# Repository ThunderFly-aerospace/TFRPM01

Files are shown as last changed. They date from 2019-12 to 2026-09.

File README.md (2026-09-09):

<a href="https://certification.oshwa.org/cz000009.html" title="Open Source Hardware Association Certificate">Open Source Hardware Association Certificate</a>

# TFRPM01 - RPM Measuring UAV Avionics Device

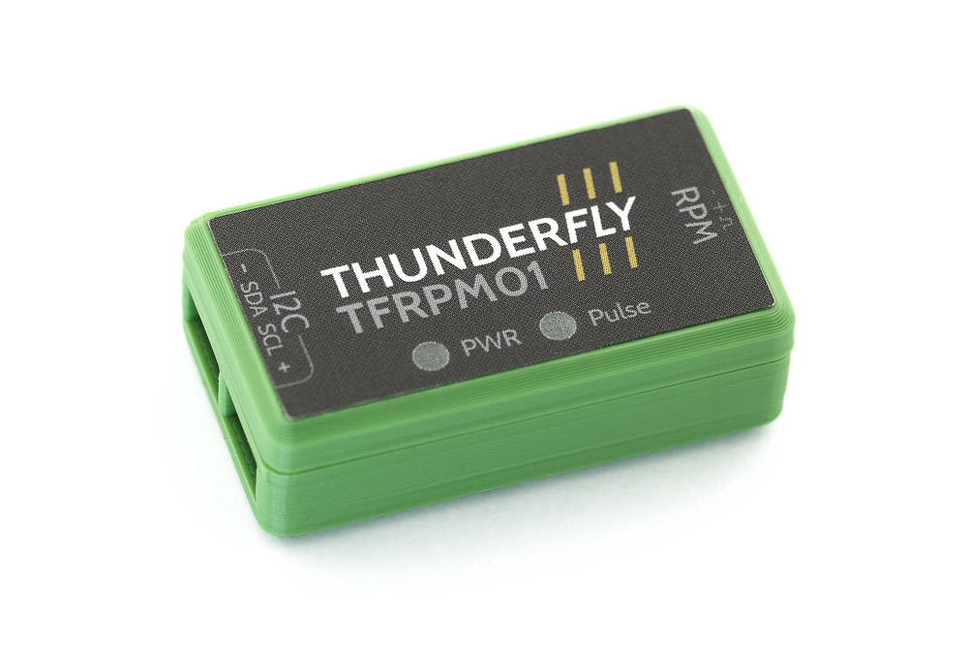
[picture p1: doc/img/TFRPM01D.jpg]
Top view on I2C RPM sensor


## Overview
The TFRPM is designed to measure revolutions per minute (RPM) in UAVs. It connects directly to Pixhawk controllers like CUAV V5+ or Holybro Pixhawk 6X via a [standard I²C connector](https://github.com/pixhawk/Pixhawk-Standards/blob/master/DS-009%20Pixhawk%20Connector%20Standard.pdf) and has the driver in PX4 firmware.

## Specifications

### Features
- **Schmitt Trigger Input**: To shape non-uniform signals from RPM sensing elements.
- **Self-Counting and Memory**: Offloads the flight controller's MCU.
- **LED Indicator**: Optionally visible in daylight for input status.
- **Protection**: Short-circuit protection on the probe connector.
- **I²C Connectors**: Pass-through connectors for daisy-chaining sensors.
- **Design**: Robust and repairable.

### Technical Parameters
- **Pulse Frequency Range**: 0 - 20 kHz.
- **I2C Connector**: 2x 4-pin JST-GH.
- **RPM Connector**: 3-pin 2.54mm pitch header.
- **I2C Address**: 0x50 default, alterable to 0x51.
- **Operating Temperature**: −20°C to +40°C.
- **Input Voltage**: +3.6V to +5.4V.
- **Mass**: 12g (4g PCB + 8g case).
- **Dimensions**: Case - 23.5x42x12.5mm, PCB - 37.5x19mm.
- **Weather Resistance**: IP40.

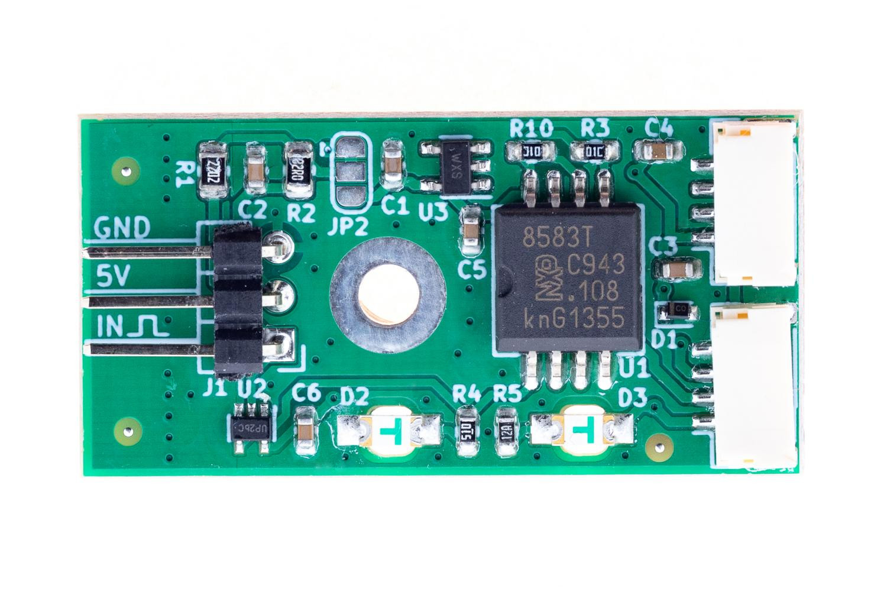
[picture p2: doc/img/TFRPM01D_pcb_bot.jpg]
Bottom view on I2C RPM sensor




### Where to Get It?
TFRPM can be bought directly from ThunderFly via [email contact](https://www.thunderfly.cz/contact-us.html). The email can also be used if there are specific requirements for custom modifications or if the product will be inquired in significant quantities. TFRPM is also available for online purchase through the [Tindie store](https://www.tindie.com/products/thunderfly/tfrpm01-drone-rpm-tachometer-sensor/).

### Connection to Pixhawk Autopilot
Follows the [Pixhawk connector standard](https://github.com/pixhawk/Pixhawk-Standards/blob/master/DS-009%20Pixhawk%20Connector%20Standard.pdf) with specific color coding.

### I²C Address Configuration
The default address is 0x50, changeable to 0x51.

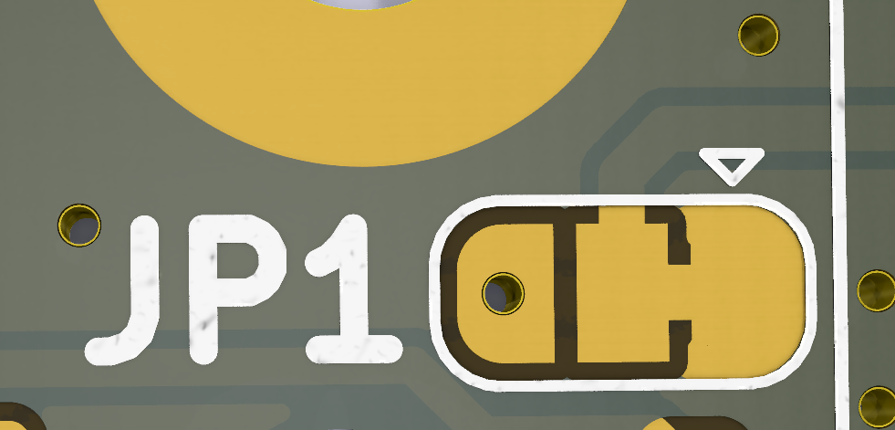
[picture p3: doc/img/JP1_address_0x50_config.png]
The default 0x50 address setup


### Mounting Options
The device can be mounted with or without a provided 3D-printed case.

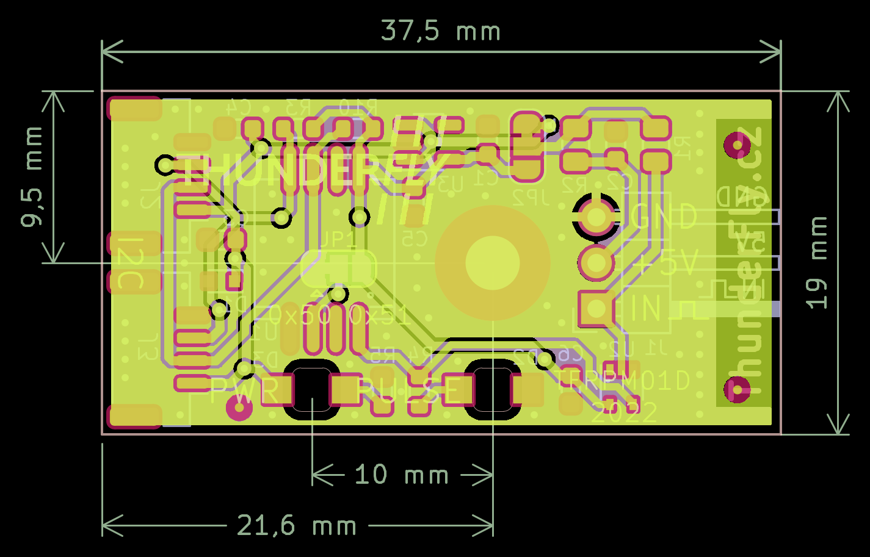
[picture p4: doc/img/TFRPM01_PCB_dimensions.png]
TFRPM01 PCB dimensions


### Sensor Probe Selection

Compatible with multiple probe types, including Hall effect and optical probes. See the [TFPROBE01](https://github.com/ThunderFly-aerospace/TFPROBE01) and [TFRPM01 documentation](https://docs.thunderfly.cz/avionics/TFRPM01/) for details.

Third-party hall probe sensors could also be used; here is an example of a suitable generic hall probe with a mounting flange.
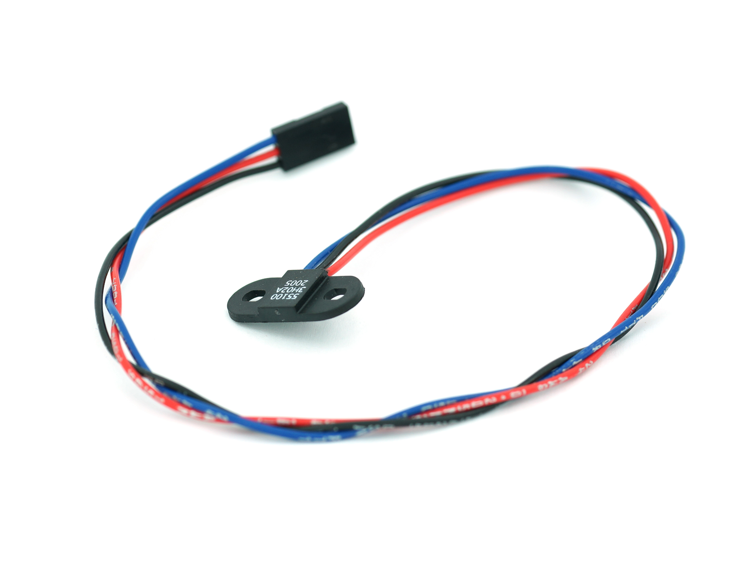
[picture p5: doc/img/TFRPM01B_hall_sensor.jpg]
TFRPM01B hall effect magnetic sensor


## Software Configuration

Supported by PX4 firmware. Setup instructions are available in the [PX4 documentation](https://docs.px4.io/main/en/sensor/thunderfly_tachometer.html#software-setup).

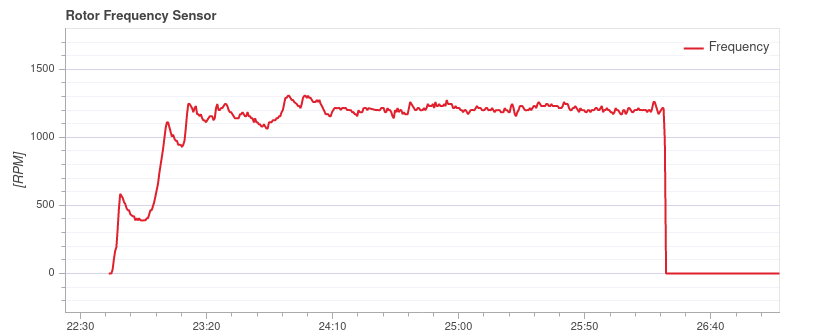
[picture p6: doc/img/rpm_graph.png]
TFRPM01 measuring rotor RPM during the flight


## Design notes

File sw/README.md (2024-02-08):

# TFRPM01 testing and demonstration software  

## Prerequisites

Expected Linux kernel module: i2c_dev

## Build

Set the Bus and Address in the source code.

    gcc rtc_1.c i2c_functions.c

# TFRPM01 interactive testing utility

The testing utility used to verify proper function of TFRPM01 device. The utility needs the following elementary testing rig for proper function. 

## Prerequirements
* python3
* [pymlab](https://github.com/MLAB-project/pymlab) with installed I2C drivers e.g. smbus2
* [beepy](https://pypi.org/project/beepy/)
* curses
* argparse

## Usage:

```
cd pymlab_interactive
python3 quality_check.py --port 9 --address 0x50 --req_freq 489 --max_deviation 10
```

`--port` smbus port
`--address` I2C address of TFRPM counter
`--req_freq`
`--max_deviation`

## Screenshots
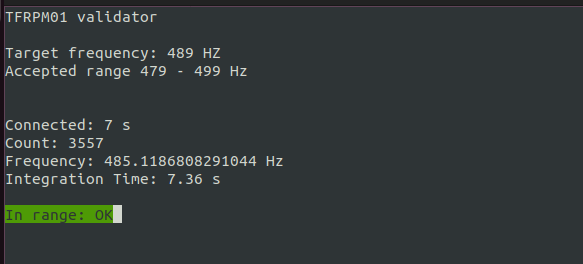
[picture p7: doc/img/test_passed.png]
Valid test


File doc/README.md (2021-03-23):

### Daylight visibility of Pulse indicating LED

The Pulse indicator LED is covered by semi-transparent sticker by default. The sticker covers the LED hole agains dust and particullary to highly unwanted water or ice dropplets. 

The sticker at same time reduce visibility of the LED. Althought the device is designed for maximal visibility of indicator LED possible it should be insuficcient in some daylight conditions. 
For that case we suggest carefully dismount the lid from the TFRPM01 and punch the sticker from outside to in the the plastic case. 
This dramatically increase the LED visibility.

Please note that change is considered as product modification and therefore the TFRPM01 could not be returned. You can always use the [TFRPM01 case model](hw/CAD/stl/RPM_case.stl) and print the case without stickers, therefore save the original ones from damage.

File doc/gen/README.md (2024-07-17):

# PCB

Board size: 37.5x19.0 mm (1.48x0.75 inches)

- This is the size of the rectangle that contains the board
- Thickness: 1.6 mm (63 mils)
- Material: FR4
- Finish: None
- Layers: 2
- Copper thickness: 35 µm

Solder mask: TOP / BOTTOM

- Color: Green

Silk screen: TOP / BOTTOM

- Color: White

Stackup:

| Name | Type | Color | Thickness | Material | Epsilon_r | Loss tangent |
|---|---|---|---|---|---|---|
| F.SilkS | Top Silk Screen | | | | | |
| F.Paste | Top Solder Paste | | | | | |
| F.Mask | Top Solder Mask | Green | 10 | | | |
| F.Cu | copper | | 35 | | | |
| dielectric 1 | core | | 1510 | FR4 | 4.5 | 0.020 |
| B.Cu | copper | | 35 | | | |
| B.Mask | Bottom Solder Mask | Green | 10 | | | |
| B.Paste | Bottom Solder Paste  | | | | | |
| B.SilkS | Bottom Silk Screen | | | | | |

# Important sizes

Clearance: 0.2 mm (8 mils)

Track width: 0.4 mm (16 mils)

- By design rules: 0.15 mm (6 mils)

Drill: 0.5 mm (20 mils)

- Vias: 0.5 mm (20 mils) [Design: 0.4 mm (16 mils)]
- Pads: 1.1 mm (43 mils)
- The above values are real drill sizes, they add 0.1 mm (4 mils) to plated holes (PTH)

Via: 0.8/0.4 mm (31/16 mils)

- By design rules: 0.4/0.3 mm (16/12 mils)
- Micro via: yes [0.2/0.1 mm (8/4 mils)]
- Buried/blind via: yes
- Total: 63 (thru: 63 buried/blind: 0 micro: 0)

Outer Annular Ring: 0.15 mm (6 mils)

- By design rules: 0.3 mm (12 mils)

Eurocircuits class: 4B
- Using min drill 0.5 mm for an OAR of 0.15 mm

# General stats

Components count: (SMD/THT)

- Top: 0/1 (THT)
- Bottom: 23/1 (SMD + THT)

Defined tracks:

- 0.3 mm (12 mils)
- 0.4 mm (16 mils)
- 0.5 mm (20 mils)
- 1.0 mm (39 mils)

Used tracks:

- 0.4 mm (16 mils) (49) defined: yes
- 0.5 mm (20 mils) (71) defined: yes

Defined vias:

Used vias:

- 0.8/0.4 mm (31/16 mils) (Count: 63, Aspect: 2.0 A) defined: no

Holes (excluding vias):

- 1.0 mm (39 mils) (3)
- 3.0 mm (118 mils) (1)

Oval holes:

Drill tools (including vias and computing adjusts and rounding):

- 0.5 mm (20 mils) (63)
- 1.1 mm (43 mils) (3)
- 3.1 mm (122 mils) (1)

Solder paste stats:

Using a paste with 87.75 % alloy, that has an specific gravity for the alloy of 7.4 g/cm³
and 1.0 g/cm³ for the flux. This paste has an specific gravity of  4.15 g/cm³.

The stencil thickness is  0.12 mm.

| Side | Pads with paste | Area [mm²] | Paste [g] |
|---|---|---|---|
| Total  | 60 | 68.18 | 0.34 |

Note: this is just an approximation to the theoretical value. Margins of the solder mask and waste aren't computed.

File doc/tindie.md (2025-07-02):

# General Description

TFRPM01 is an open-source frequency sensor [tachometer](https://en.wikipedia.org/wiki/Tachometer) intended for the measurement of the speed of rotational actuators on drones. The TFRPM01 sensor itself does not contain a sensing probe. It needs to be connected externally. This allows you to connect many different probes based on different technologies. For basic diagnostics, the sensor is equipped with an LED indicator that shows the logic state of the input pin.

TFRPM01 is supported by Pixhawk autopilots with up-to-date PX4 firmware. For the correct setting of the sensor, see the [official documentation](https://docs.px4.io/master/en/sensor/thunderfly_tachometer.html). The sensor is designed to be able to count high frequencies without overloading the autopilot CPU.

# Technical description

The sensor is based on I²C pulse counter IO [PCF8583](https://www.nxp.com/docs/en/data-sheet/PCF8583.pdf). 

The I2C connector is a 4-pin JST-GH connector compliant with [Pixhawk Reference Standards](https://pixhawk.org/standards/). The second I2C connector can be used as a thought-pass I2C output and allows to connection of another sensor on the same bus. 

There can be up to two TFRPM sensors on one bus. The default sensor address is 0x50 and it can be changed to 0x51 by the use of soldering iron. A sensor with a different address is available on request.

For connecting the probe, the sensor is equipped with a standard three-pin header connector. The connector contains a power and signal pin. The order of pins is GND 5V Signal. It supports 5V TTL signals. The maximum pulse frequency of IO is 20 kHz with a 50% duty cycle. Maximal measured frequency and accuracy depend on the driver setting.

# Supported probes

## Hall-Effect Sensor Probe

Hall-effect sensors (magnetically operated) are ideal for harsh environments, where dirt, dust, and water can contact the sensed rotor.

Many different hall-effect sensors are commercially available. For example, a 5100 Miniature Flange Mounting Proximity Sensor is a good choice. 

Example of Hall effect probe Hall effect probe

## Optical Sensor Probe

The optical sensor can also be used (and maybe is a better fit, depending on the measurement requirements). Both transmissive and reflective sensor types may be used for pulse generation. We suggest the [TFPROBE01](https://docs.thunderfly.cz/avionics/TFRPM01/probe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) reflective optical sensor, which is combined with optional magnetic sensing. 

Optical Sensor Probe Optical sensor probe

# PX4 configuration

How to set up the TRRPM01 sensor with [PX4](https://px4.io/) based autopilot is described in [official documentation](https://docs.px4.io/master/en/sensor/thunderfly_tachometer.html). PX4 driver acquires RPM frequency from the sensor and sends it as an internal uORB message. uORB message is logged in autopilot and translated to MAVLink message and can be received/visualized by a ground station (QGroundControl). 

PlotJugles screen with RPM data

The sensor was tested with CUAV V5+ and CUAV Nano autopilot. Other PX4-based autopilots should be also supported with PX4 firmware.

## Use of multiple TFRPM01 sensors

In applications where multiple TFRPM01 are needed, the [TFI2CADT01](https://www.tindie.com/products/26353/) module could be used. That allows the connection of up to six TFRPM01s to a single I2C port.

Multiple sensors

# The package includes:
- TFRPM01D
- Plastic case

## Optionally
- [I2C silicone cable](https://www.tindie.com/products/30113/) (TFCABxxI2C01) in lengths of 15cm, 30cm, 40cm
- [Sensing probe](https://docs.thunderfly.cz/avionics/TFRPM01/probe) (TFPROBE01 or Hall probe 55100)

# Accessories

## I2C cables
You may need to purchase additional [I2C cables separately](https://www.tindie.com/products/30113/). We offer high-quality cables that are compatible with the [Pixhawk standard](https://raw.githubusercontent.com/pixhawk/Pixhawk-Standards/master/DS-009%20Pixhawk%20Connector%20Standard.pdf) and with a [ThunderFly color scheme](https://docs.px4.io/main/en/assembly/cable_wiring.html#i2c-cables) for easy signal type identification. ThunderFly cables are specifically designed with improved resistance to electromagnetic interference and a silicone insulator that makes them highly flexible.

  * [TFCAB15I2C01](https://docs.thunderfly.cz/avionics/TFCAB01/) [Buy at Tindie](https://www.tindie.com/products/30113/)

## Sensor probe
The [sensing probe](https://docs.thunderfly.cz/avionics/TFRPM01/probe) is not included in the TFRPM01 sensor package. ThunderFly sells and has tested the following two probes, which can be directly connected to the TFRPM01 sensor board:

  * Hall probe with flange
  * [TFPROBE01 - Omnipolar magnetic and reflective optical probe](https://www.tindie.com/products/27741/)

# Product changelog
The product is gradually evolving and improving based on user requirements. Currently (as of 05/2023), the TFRPM01D revision is being shipped. In the development process, we keep backward compatibility, for example by keeping the same form factor or communication interface. The complete list of changes is in [releases](https://github.com/ThunderFly-aerospace/TFRPM01/releases).

#### TFRPM01D (from 06/2023)
Roll-back to sticker version with a hole for the screw, to allow user disassembly. 

#### TFRPM01D (from 05/2023)
 * Green case
 * Added an LED indicating the sensor power supply
 * Improved PCB layout

Note: The TFRPM01D sensors shipped from 8. 5. 2023 does not have a hole in the bottom sticker for accessing the screw for disassembling the plastic case. To change the I2C device address or output voltage, it is necessary to remove the bottom sticker and unscrew the screw. (The bottom sticker is a sticker with a QR code)

#### TFRPM01C (from 03/2021) 
 * Gray case
 
#### TFRPM01B (from 12/2020)
 * Orange case

#### TFRPM01A - Was not publicly available

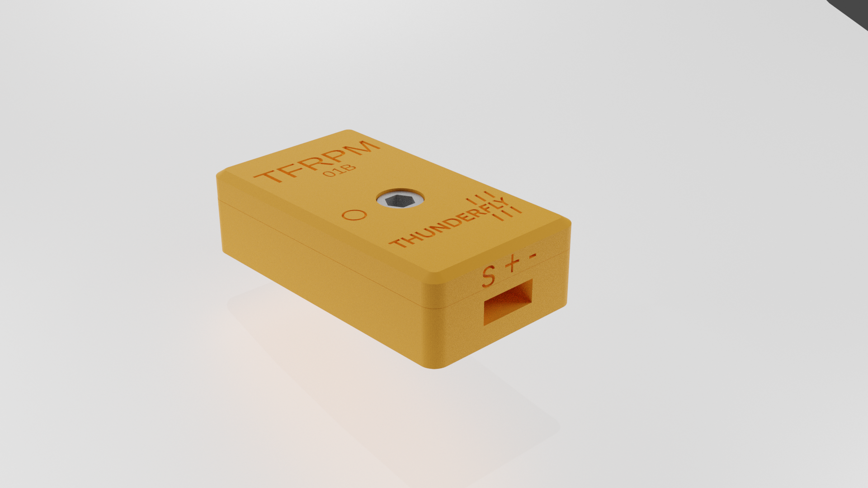
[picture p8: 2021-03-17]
hw/render/out/TFRPM01_001.png

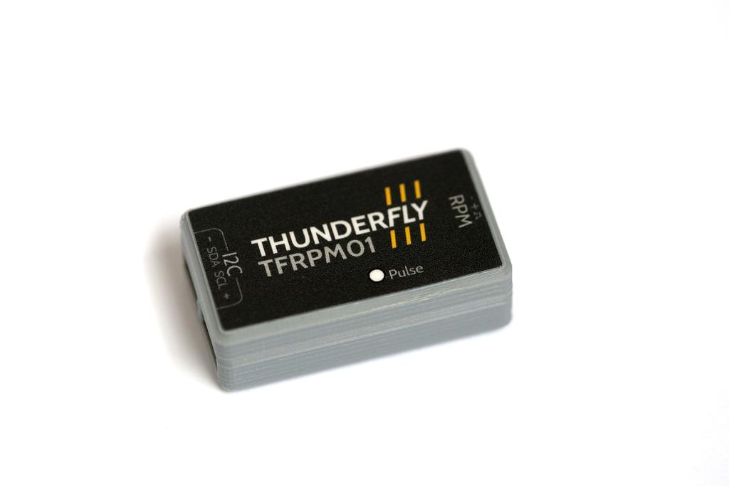
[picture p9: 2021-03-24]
doc/img/TFRPM01C_case.jpg

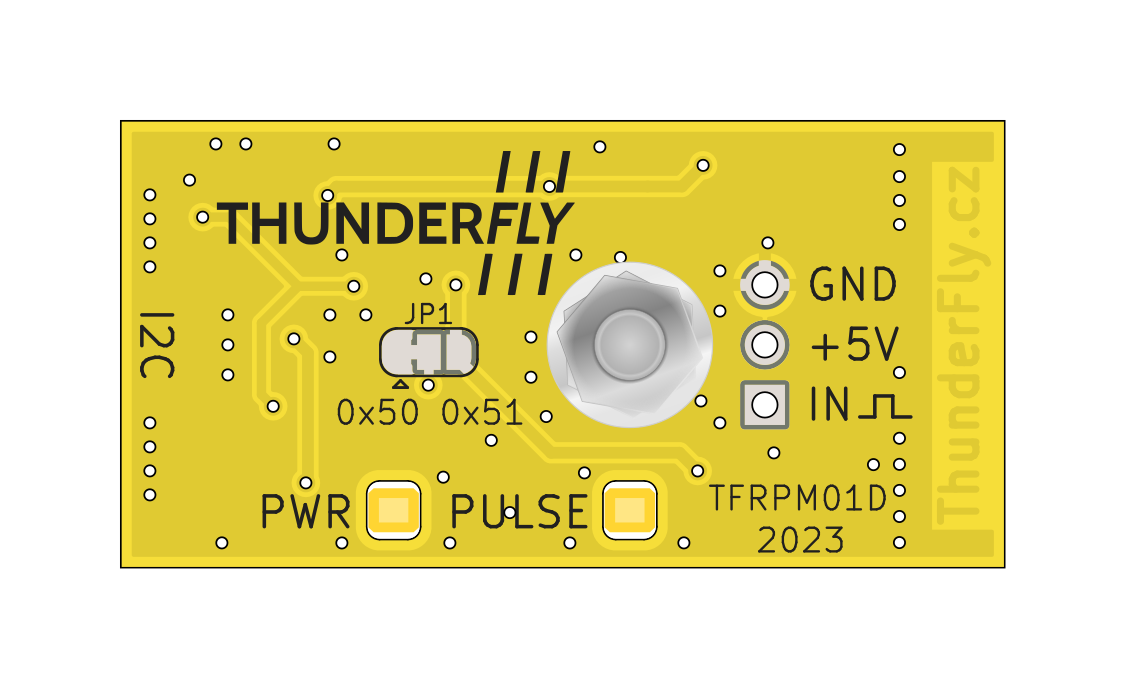
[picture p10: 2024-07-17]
doc/gen/img/TFRPM01-top.png

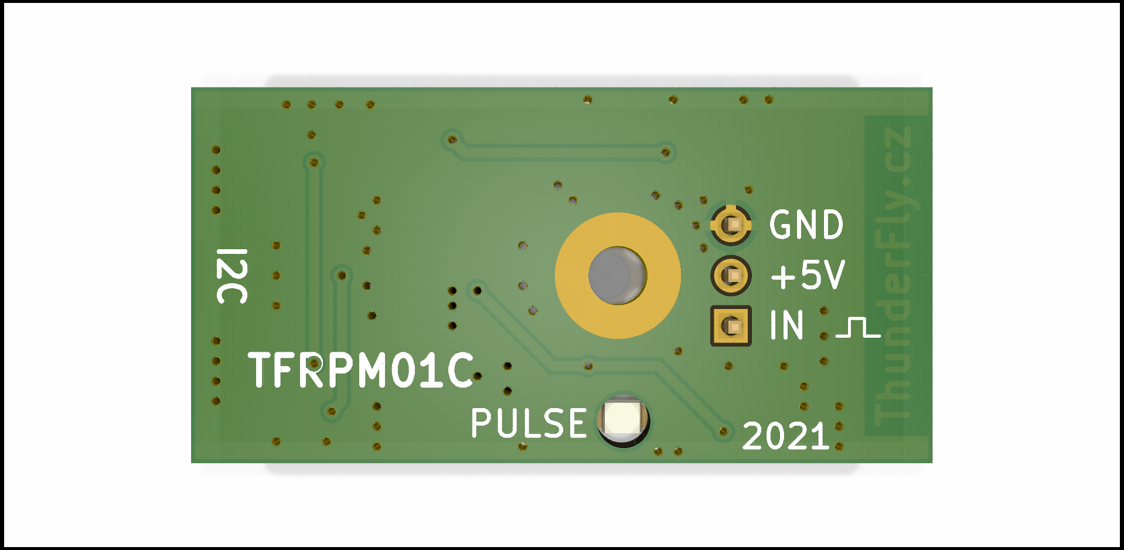
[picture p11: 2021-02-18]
doc/img/TFRPM01C_top_big.png

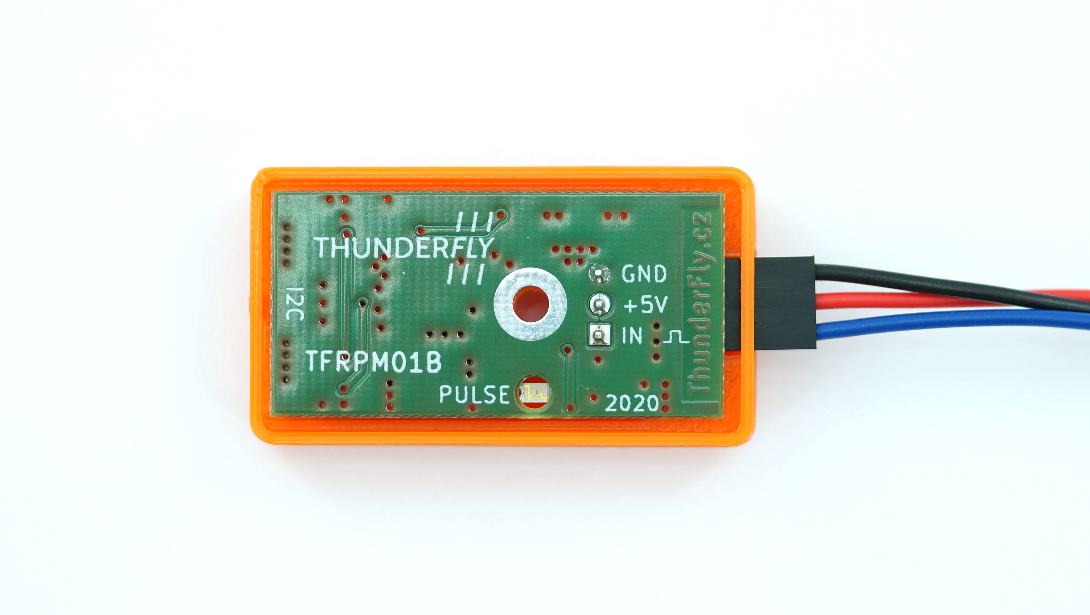
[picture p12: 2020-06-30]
doc/img/TFRPM01B_hall_connection.jpg

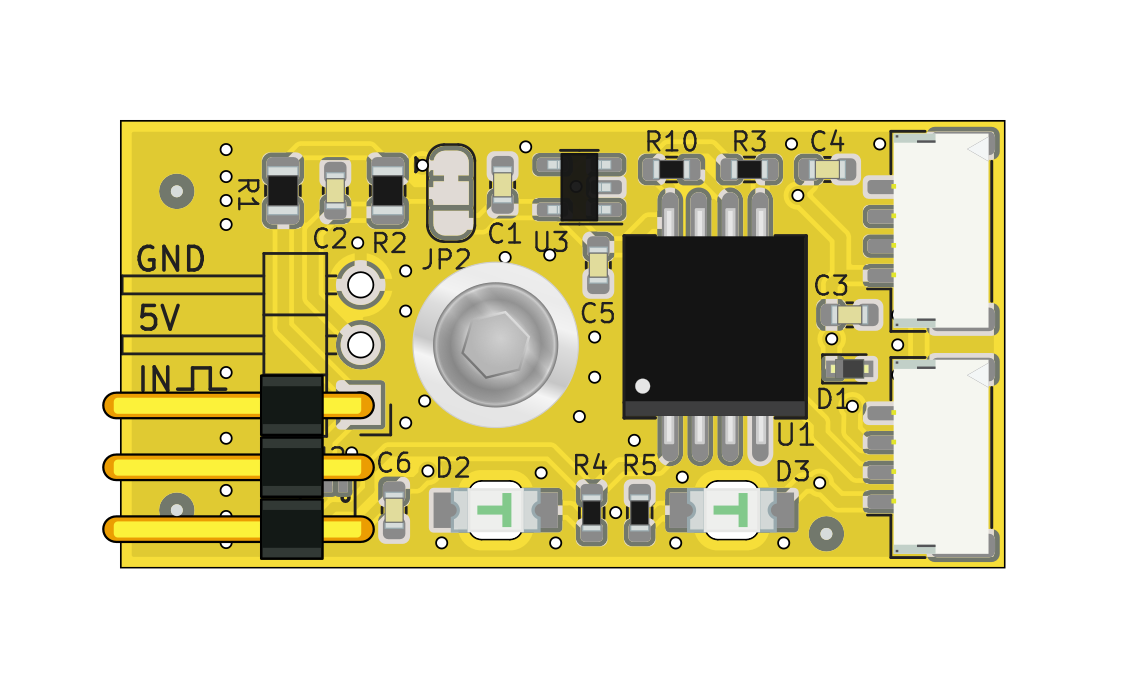
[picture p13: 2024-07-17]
doc/gen/img/TFRPM01-bottom.png

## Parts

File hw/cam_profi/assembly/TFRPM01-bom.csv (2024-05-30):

Component | Description | Part | References | Value | Footprint | Quantity Per PCB | Datasheet | ust_id | color
1 | Unpolarized capacitor | C | C4C5C6 | 100nF | C_0603_1608Metric | 3 | ~ | 5c70984812875079b91f8bf2
2 | Unpolarized capacitor | C | C1 | 1uF | C_0603_1608Metric | 1 | ~ | 5c70984812875079b91f8bc2
3 | Unpolarized capacitor | C | C2C3 | 10uF | C_0603_1608Metric | 2 | ~ | 5c70984812875079b91f8bf5
4 |  | D_ZENER | D1 | BZX585-B5V6.115 | D_SOD-523 | 1 |  | 60879d38128750769ee58e48
5 | Light emitting diode | LED | D3 | KPTR-3216CGCK | LED_1206_2 | 1 | ~ |  | Green
6 | Light emitting diode | LED | D2 | KPTR-3216SURCK | LED_1206_2 | 1 | ~ |  | Red
7 | 1x03 2.54 mm pitch header | HEADER_1x03 | J1 | DS1022-1*40RDF11-B | PinHeader_1x03_P2.54mm_Horizontal | 1 | 5c70984412875079b91f879d
8 |  | SM04B-GHS-TB_1 | J2 | SM04B-GHS-TB | JST_GH_SM04B-GHS-TB_1x04-1MP_P1.25mm_Horizontal | 1 |  | 5c86273d1287500b4e0280be
9 |  | SM04B-GHS-TB | J3 | SM04B-GHS-TB | JST_GH_SM04B-GHS-TB_1x04-1MP_P1.25mm_Horizontal | 1 |  | 5c86273d1287500b4e0280be
10 | Resistor | R | R4 | 51R | R_0603_1608Metric | 1 | ~ | 5c70984512875079b91f8953
11 | Resistor | R | R2 | 82R | R_0805_2012Metric | 1 | ~ | 5c70984512875079b91f8976
12 | Resistor | R | R5 | 130R | R_0603_1608Metric | 1 | ~ | 5cd08b17128750448e4542b1
13 | Resistor | R | R3R10 | 10k | R_0603_1608Metric | 2 | ~ | 5c70984512875079b91f8962
14 | Resistor | R | R1 | 22k | R_0805_2012Metric | 1 | ~ | 5c70984712875079b91f8a87
15 | 300mA Low-dropout Voltage Regulator, Vout 3.3V, Vin up to 5.5V, SOT-23 | MIC5504-3.3YM5 | U3 | MIC5504-3.3YM5 | SOT-23-5 | 1 | http://ww1.microchip.com/downloads/en/DeviceDoc/MIC550X.pdf | 5c7255e81287500b4e112ea2
16 |  | PCF8583 | U1 | PCF8583T | SOT176-1 | 1 | https://www.nxp.com/docs/en/data-sheet/PCF8583.pdf | 5c70984712875079b91f8b59
17 | Hex inverter schmitt trigger | 74AHC1G14GV | U2 | SN74LVC1G14QDCKRQ1 | SOT-353_SC-70-5 | 1 | http://www.ti.com/lit/gpn/sn74HC14 | 604b05e1128750769e5b106e

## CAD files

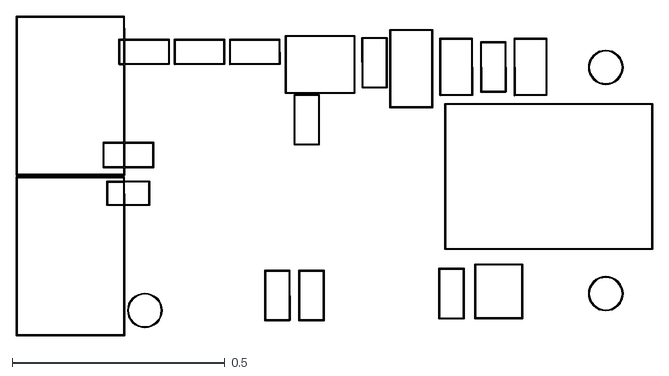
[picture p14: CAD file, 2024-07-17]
doc/gen/dxf/TFRPM01-B_Courtyard.dxf
1.49 x 0.751

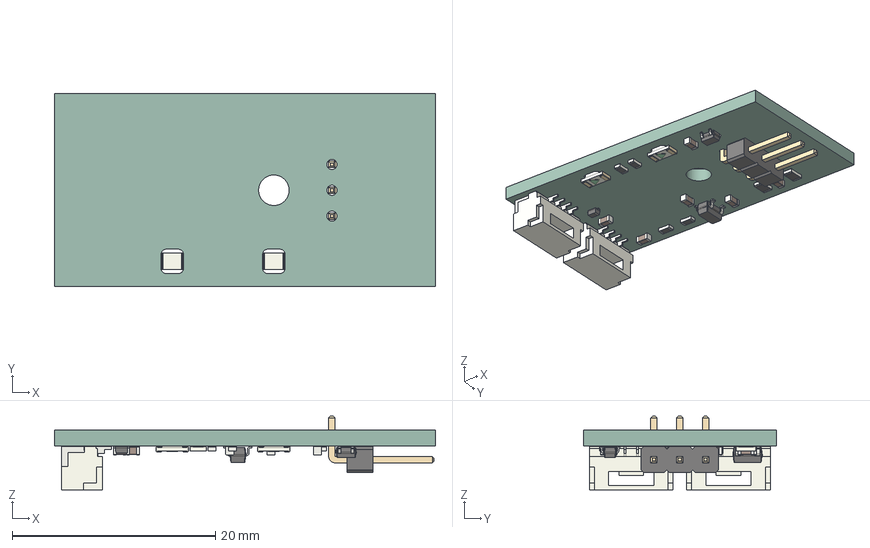
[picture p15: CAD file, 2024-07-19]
doc/gen/TFRPM01.step
37.5 x 19.0 x 7.25 mm
D_SOD_523
R_0603_1608Metric x 4
PinHeader_1x03_P254mm_Horizontal
SOT_23_5
C_0603_1608Metric x 6
JST_SM04B_GHS_TB x 2
R_0805_2012Metric x 2
LED_1206_3216Metric x 2
SOT_353_SC_70_5
kibot_prf3_h6c_PCB

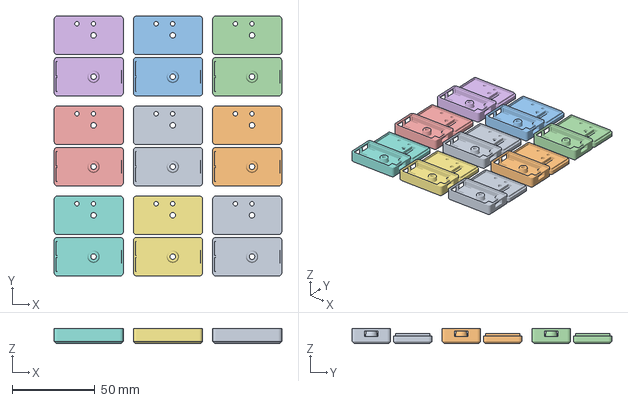
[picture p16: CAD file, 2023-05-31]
hw/CAD/stl/RPM_case_multi_Prusa_project.3mf
137.7 x 157.2 x 9.00 mm

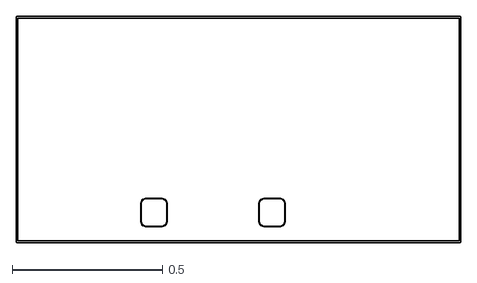
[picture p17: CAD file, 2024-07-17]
doc/gen/dxf/TFRPM01-Edge_Cuts.dxf
1.48 x 0.754

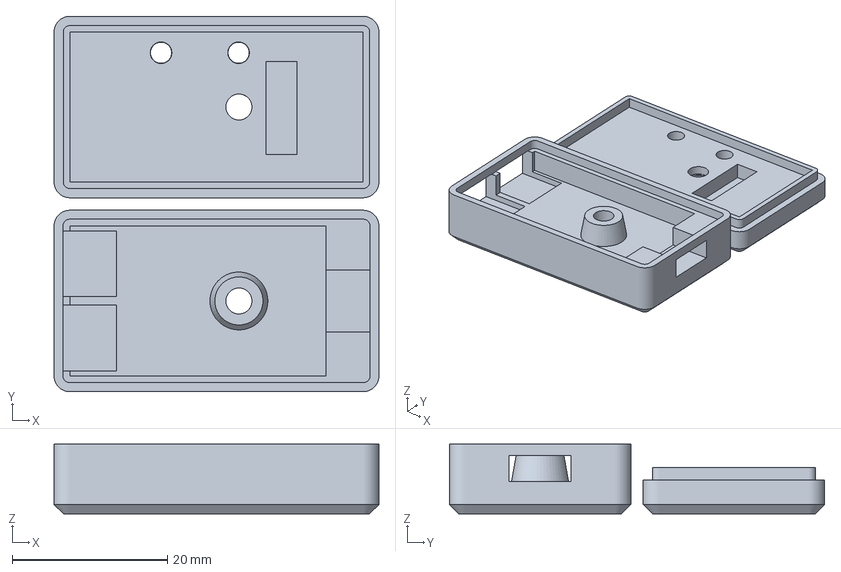
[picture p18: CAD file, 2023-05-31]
hw/CAD/stl/RPM_case_Prusa_project.3mf
41.9 x 48.4 x 9.00 mm

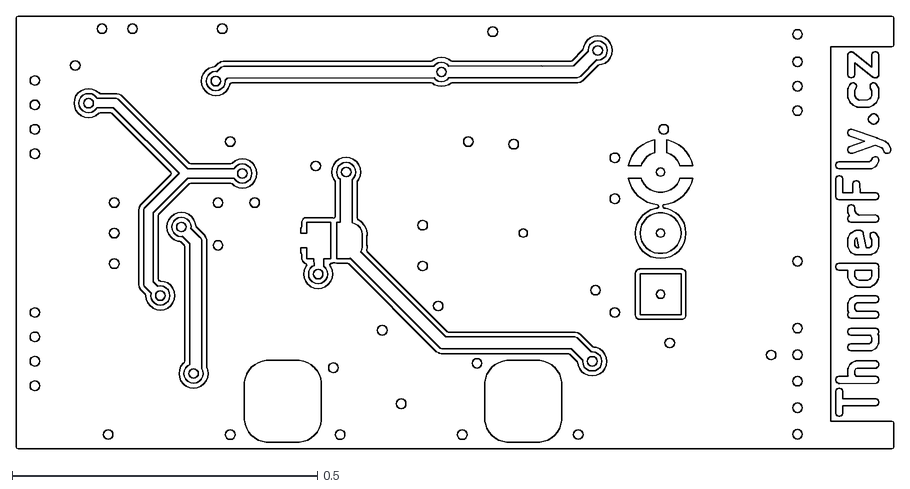
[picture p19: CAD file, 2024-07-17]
doc/gen/dxf/TFRPM01-F_Cu.dxf
1.44 x 0.709

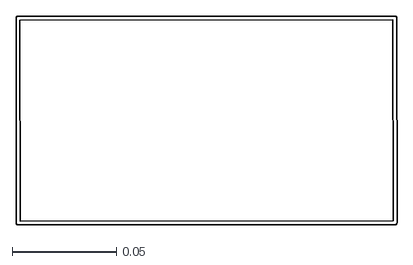
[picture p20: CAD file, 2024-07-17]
doc/gen/dxf/TFRPM01-F_Courtyard.dxf
0.183 x 0.1

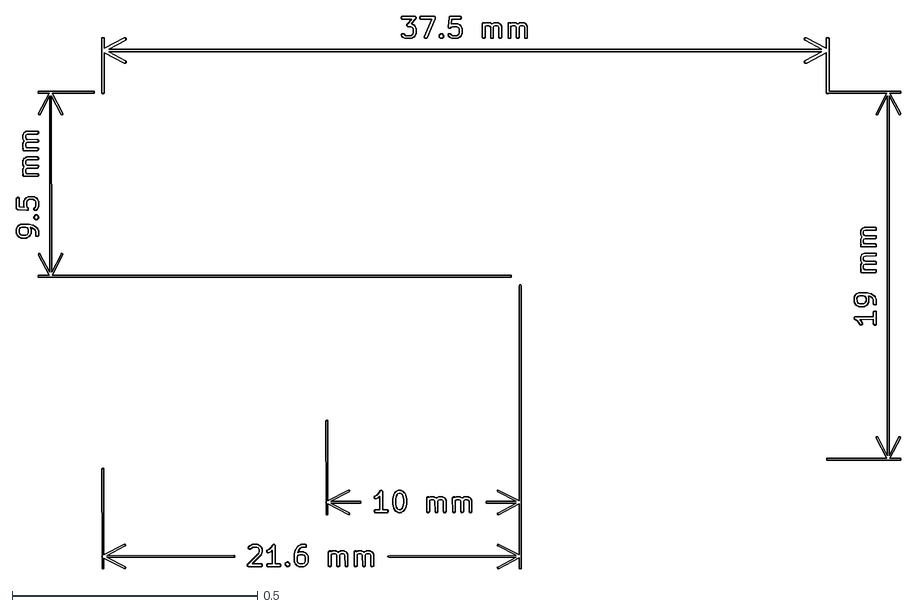
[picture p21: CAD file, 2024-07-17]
doc/gen/dxf/TFRPM01-User_Drawings.dxf
1.80 x 1.13

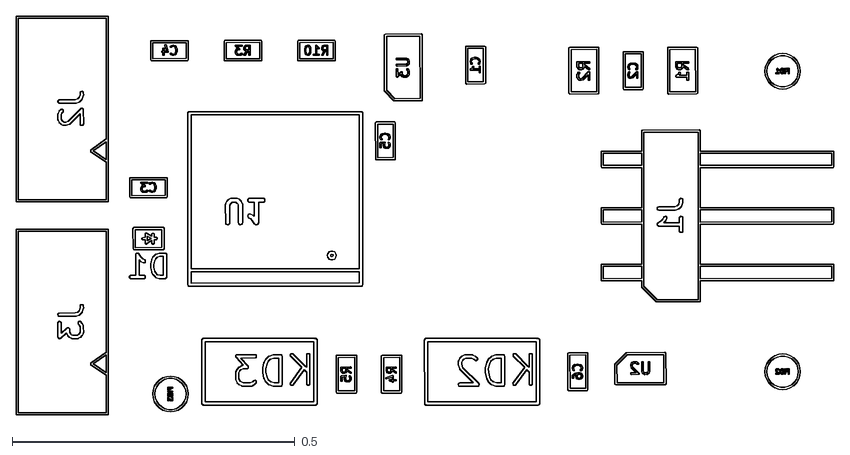
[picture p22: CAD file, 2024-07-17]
doc/gen/dxf/TFRPM01-B_Fab.dxf
1.45 x 0.706

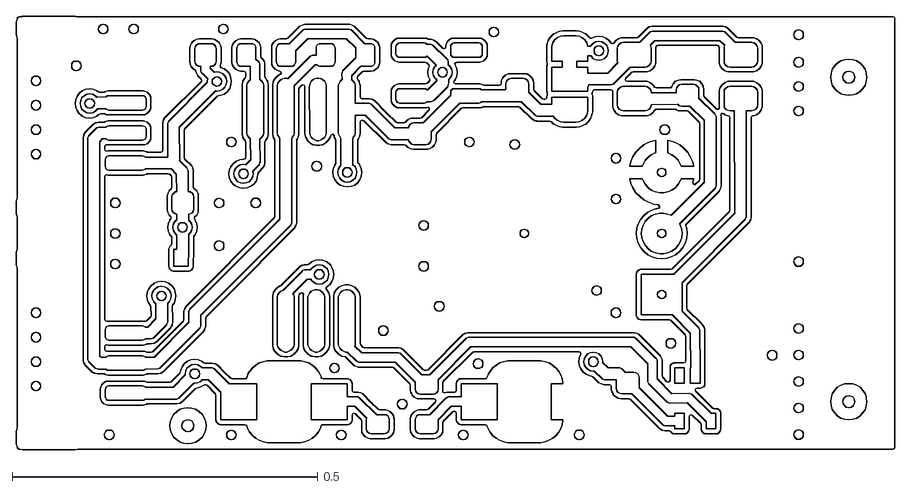
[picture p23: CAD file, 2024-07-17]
doc/gen/dxf/TFRPM01-B_Cu.dxf
1.44 x 0.71

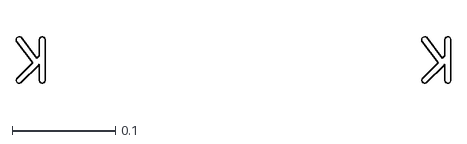
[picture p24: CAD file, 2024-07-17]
doc/gen/dxf/TFRPM01-F_Fab.dxf
0.422 x 0.0452

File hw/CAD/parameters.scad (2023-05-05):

layer_thickness = 0.2;
global_clearance = 0.5;

tolerance = 0.3;

screw_dist = 21.6 + tolerance/2; // vzdalenost sroubu od jedne hrany PCB

case_brim = 0.82;  // limec okolo PCB
case_wall = 0.41*3;

pcb_l = 37.5 + tolerance;
pcb_w = 19.0 + tolerance;
pcb_t = 1.6;

M3_screw_diameter = 3.35;
M3_screw_head_height = 3.2;
M3_screw_lenght = 10;
M3_head_diameter = 6.3;
M3_nut_diameter = 6.5;
M3_nut_height = 3;

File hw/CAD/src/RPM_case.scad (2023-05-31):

include<../parameters.scad>
use<lib/stdlib/bolts.scad>

module rpm_case_top(){

    difference(){
        union(){
            hull(){
                translate([0,0, -M3_screw_head_height])
                    minkowski(){
                       cube([pcb_l, pcb_w, 2]);
                       cylinder(d= 2*case_wall + 2*case_brim, h = M3_screw_head_height-2, $fn=50);
                    }

                translate([0, 0, -M3_screw_head_height - 6*layer_thickness])
                    minkowski(){
                       cube([pcb_l, pcb_w, 1]);
                       cylinder( d=2*case_brim , h = 2-1, $fn=50);
                    }
            }
            minkowski(){
               cube([pcb_l, pcb_w, 0.5]);
               cylinder(d=2*case_brim + global_clearance/7, h = pcb_t-0.5, $fn=50); // global_clearance/7 improve fit of case top and bottom.
            }
        }

        // Otvor pro PCB
        translate([0, 0, 0])
            cube([pcb_l, pcb_w, 10]);

        // Otvory pro sroubek
        //#translate([screw_dist, pcb_w/2, - M3_screw_head_height - 8*layer_thickness - 5])
        //    rotate(30) cylinder(d = M3_nut_diameter, h = M3_screw_head_height+5, $fn = 6);
        translate([21.79, pcb_w/2, - M3_screw_head_height - 7*layer_thickness])
            rotate(30) cylinder(d1 = M3_nut_diameter +1, d2 = M3_nut_diameter, h = 0.5, $fn = 6);
        translate([screw_dist, pcb_w/2, - M3_screw_head_height - 6.9*layer_thickness - 5])  difference(){   
                    rotate(30) cylinder(d = M3_nut_diameter, h = M3_screw_head_height+5, $fn = 6); // screw head hole .... Try to do fancy hole .. :) without support
                    for( x = [[0, 0], [60, 0.15], [120, 0.30]]) translate([0, 0, -x[1] + M3_screw_head_height + 5 ]) rotate([0, 0, x[0]]) {
                        translate([M3_screw_diameter/2, -5, 0]) cube([10, 10, 0.2]);
                        translate([-10-M3_screw_diameter/2, -5, 0]) cube([10, 10, 0.2]);
                    }
                }
            
        translate([21.79, pcb_w/2, - 7*layer_thickness])
            cylinder(d = M3_screw_diameter, h = 10, $fn = 50);

        // LED hole
        for(lx=[screw_dist, screw_dist-10]){
        translate([lx, pcb_w/2+7, -4.5])
            cylinder(d1 = 2.7, d2 = 2.8, h = 5, $fn = 50);
        translate([lx, pcb_w/2+7, -4.5])
            cylinder(d1 = 2.7+0.8, d2 = 2.7, h = 0.6, $fn = 50);
        }
            
        // pinheader hole
        translate([27.3, 9.525,0])
            cube([4, 12, 2.5*2], center=true);

    }
}



module rpm_case_bottom(){
    difference(){
        union(){
            hull(){
                translate([0,0, -M3_screw_head_height-3])
                    minkowski(){
                       cube([pcb_l, pcb_w, 1+3]);
                       cylinder(d=2*case_wall + 2*case_brim, h = M3_screw_head_height-1+pcb_t, $fn=50);
                    }

                translate([0, 0, -M3_screw_head_height -  6*layer_thickness - 3])
                    minkowski(){
                       cube([pcb_l, pcb_w, 1]);
                       cylinder(d=2*case_brim, h = 2-1, $fn=50);
                    }
            }


        }

        translate([0, 0, -layer_thickness + 0.3])
          minkowski(){
             cube([pcb_l, pcb_w, 1]);
             cylinder(d=2*case_brim+0.15, h = pcb_t, $fn=50);
          }
        // sensor PCB
        difference(){
            translate([0, 0, -3.5])
                cube([pcb_l, pcb_w, 10]);
            translate([21.79, pcb_w/2, -10])
                cylinder(d1 = M3_nut_diameter*1.5, d2 = 6.2, h = 10 - layer_thickness + 0.3, $fn = 50);
            translate([33, 0, -5])
                cube([pcb_l, pcb_w, 6]);
        }
        // Pinheader
        translate([27.3+10, pcb_w/2,-1.55])
            cube([20, 8, 3.3], center=true);

        // Vyrezy pro tisk
        /* translate([27.3+5, 2,-1.55])
            cube([10, 5, 5.2], center=true);
        translate([27.3+5, pcb_w-2,-1.55])
            cube([10, 5, 5.2], center=true);
        translate([13, pcb_w/2,-1.55])
            cube([8, pcb_w+1, 5.2], center=true); */


        // I2C connectors
        translate([-6, 0.6, -4.35 - 0.15])
            cube([12, 9-0.5, 4.35 + 0.3]);
        translate([-6, pcb_w - 9.1, -4.35 - 0.15])
            cube([12, 9-0.5, 4.35 + 0.3]);

        // screw
        translate([21.79, pcb_w/2, -2 + 0.15]){
            translate([0, 0,  -M3_screw_head_height -  6*layer_thickness -3 + 2 - layer_thickness]){
                translate([0, 0, M3_screw_head_height]) cylinder(d = M3_screw_diameter, h = 10, $fn = 50); // screw hole
                translate([0, 0, 0]) difference(){   
                    cylinder(d = M3_head_diameter, h = M3_screw_head_height, $fn = 50); // screw head hole .... Try to do fancy hole .. :) without support
                    for( x = [[0, 0], [60, 0.15], [120, 0.30]]) translate([0, 0, -x[1]]) {
                        rotate([0, 0, x[0]]) translate([M3_screw_diameter/2, -5, M3_screw_head_height]) cube([10, 10, 0.2]);
                        rotate([0, 0, x[0]]) translate([-10-M3_screw_diameter/2, -5, M3_screw_head_height]) cube([10, 10, 0.2]);
                    }
                }
                translate([0, 0, 0]) cylinder(d1 = M3_head_diameter+1, d2 = M3_head_diameter, h = 0.6, $fn = 50); // hole bevel
            }

         }
    }
}

if(1){
    rpm_case_top();
    translate([0, -25, 3])
        rpm_case_bottom();
}


if(0) projection(cut=true) translate([0, 0, 4.15]) {
    rpm_case_top();

    translate([0, -30, 3])
        rpm_case_bottom();
}

if(0){
    rpm_case_top();

    translate([0, pcb_w, pcb_t+0.1])
        rotate([180, 0, 0])
            rpm_case_bottom();
}

use <../../../doc/sticker/sticker_outline.scad>

//translate([19, -32.8, -5.25]) color("green", 0.5) %poly_rect1948(0.1);
//translate([19, 22.2, -5.25]) color("green", 0.5) %poly_rect1944(0.1);

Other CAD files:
doc/gen/TFRPM01D.step
hw/CAD/stl/RPM_case.stl
doc/gen/dxf/TFRPM01-Margin.dxf
doc/gen/dxf/TFRPM01-B_Mask.dxf
doc/gen/dxf/TFRPM01-B_Paste.dxf
doc/gen/dxf/TFRPM01-B_Silkscreen.dxf
doc/gen/dxf/TFRPM01-F_Mask.dxf
doc/gen/dxf/TFRPM01-F_Paste.dxf
doc/gen/dxf/TFRPM01-F_Silkscreen.dxf
hw/render/src/TFRPM.blend

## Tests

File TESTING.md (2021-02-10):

# Testování TFRPM01

## Testování s PX4 autopilotem

### Pomocí QGroundControlu
V QGC přejdete do `menu` > `Analyze tools` > `Mavlink Inspector`

Zde v levém sloupci najděte zprávu `raw_rpm`. Pokud neexistuje, je potřeba zjistit, jestli je driver senzoru spuštěný. 
Pokud se tam zpráva vyskytuje, klikněte na ní. V pravé části pak uvidíte živá data. 

### Pomocí PX4 (NuttX) konzole
Jestli máte spuštěný driver zjistíte příkazem: 
```
pcf8583 status
```
Pokud je driver spuštěn, bude vypsán port a základní nastavení spuštěné instance.  V případě že driver neběží, tak je potřeba jej spustit

The driver does not start automatically in any airframes. You can start it manually from the console or add it to the [startup script](../concept/system_startup.md#customizing-the-system-startup) on SD card.

#### Start driver from console
Start driver from the [console](https://docs.qgroundcontrol.com/master/en/analyze_view/mavlink_console.html) with the command:
```
pcf8583 start -X -b <bus number>
```
insted of `<bus number>` you must specify the bus number to which the device is connected. `-X` means that it is external bus.

:::note
Bus number `-b <bus number>` does not match the bus numbering on the autopilot. After running the command, the driver shows the bus number corresponding to the label on the box.

When using CUAV V5+ or CUAV Nano:

| bus label | -b number |
|---|---|
| 1 |  -X -b 4  |
| 2 |  -X -b 2  |
| 3 |  -X -b 1  |

:::

**Vypsání posledních měřených hodnot**
```
listener rpm -n 100
```
_parametr `-n` nastavuje počet vypsaných zpráv_

## Základní (manuální) testování
Základní testování TFRPM01 po výrobě lze provést pomocí python [skriptu](/sw/pymlab/TFRPM_readout.py) postaveném na knihovně [PyMLAB](https://github.com/MLAB-project/pymlab). 

Skript ze složky `/sw/pymlab/` spustíte příkazem:

```
sudo python3 TFRPM_readout.py 0 0x50
```

Po úspěšném spuštění by se měly objevit měřené hodnoty. Nyní, pomocí nějaké sondy nebo uzeměním signálového pinu, simulujte čitací signál. Hodnota `count` by měla růst. Pro přesnější měření lze použit signál generovaný osciloskopem nebo jiným zdrojem pilového signálu. 

Výstup pak může vypadat následovně: 

```bash
TFRPM01 test suite.
{'port': '0', 'device': None, 'serial_number': None}
counter module example 

1608153501.8307571; count: 0, freq: 0.00, integration_time: 0.03
1608153502.3609016; count: 0, freq: 0.00, integration_time: 0.56
1608153502.8917809; count: 0, freq: 0.00, integration_time: 1.09
1608153503.4219267; count: 0, freq: 0.00, integration_time: 1.62
1608153503.9529395; count: 0, freq: 0.00, integration_time: 2.15
1608153504.4839747; count: 0, freq: 0.00, integration_time: 2.68
1608153505.0149646; count: 0, freq: 0.00, integration_time: 3.21
1608153505.5448906; count: 0, freq: 0.00, integration_time: 3.74
1608153506.0749886; count: 0, freq: 0.00, integration_time: 4.27
1608153506.6050436; count: 0, freq: 0.00, integration_time: 4.80
1608153507.136024; count: 0, freq: 0.00, integration_time: 5.34
1608153507.6670556; count: 0, freq: 0.00, integration_time: 5.87
1608153508.197005; count: 0, freq: 0.00, integration_time: 6.40
1608153508.728068; count: 0, freq: 0.00, integration_time: 6.93
1608153509.2590628; count: 2, freq: 0.27, integration_time: 7.46
1608153509.7890441; count: 5, freq: 0.63, integration_time: 7.99
1608153510.3190136; count: 8, freq: 0.94, integration_time: 8.52
1608153510.8490016; count: 11, freq: 1.22, integration_time: 9.05
1608153511.3801253; count: 14, freq: 1.46, integration_time: 9.58
```

V prvním sloupci je čas. Následuje počet detekovaných signálů, určená frekvence a čas po kterou je frekvence počitána. 

## Automatické testování

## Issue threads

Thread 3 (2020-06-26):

Velikost otvoru pro matku sroubu

kaklik, 2020-06-26:
Sroub stahujici krabicku ma ve vicku sestihran pro zapusteni matice. Ten je ale moc maly a matice tam nejde vlozit.
Ma o 0.6mm mensi prumer, nez by mela mit.

Resenim zrejme je pouziti sroubu ze [standardni knihovny](https://github.com/ThunderFly-aerospace/Openscad_stdlib).

kaklik, 2020-12-09:
Pokusil jsem se použít knihovnu bolts.scad od @JanKott  Ale potíž je, že knihovna neumožňuje získat parametry rozměrů šroubu. Tudíž nelze její použití realizovat žádným přímým způsobem, neboť rozměry modelu jsou navázány na rozměry šroubu.

JanKott, 2020-12-09:
Upravim bolts knihovnu

JanKott, 2020-12-09:
Nyní jsou k dispozici funkce bolt_diameter, head_height, head_diameter, nut_height, nut_diameter, nut_pocket. Argumentem je velikost.

Closed 2020-12-09.

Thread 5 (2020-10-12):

Zvážit nastavení I2C adresy pomocí pájecích plošek

ChroustJan, 2020-10-12:
Momentálně je adresa na modulu vybrána osezením rezistoru na správnou pozici. Tohle řešení má ale podobný problém jako #4 Takže uvažuje relativně dobře vybavenou dílnu.
Domnívám se že na zákazníka je to zbytečně vysoký požadavek.

V případe přepínání adresy by možná bylo možné modul vylepšit použitím cínovací plošky.

kaklik, 2021-02-18:
Vyřešeno v rámci issue #4 přidáním cínovací plošky JP1 s default nastavením A0 na GND.

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

Closed 2021-02-18.

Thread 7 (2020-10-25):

Hall/Optical external sensor board

kaklik, 2020-10-25:
Na základě některých [nových aplikací modulu](https://github.com/ThunderFly-aerospace/TF-G2/issues/64
) by zřejmě bylo vhodné vytvořit externí plošný spoj s magnetickým a optickým snímačem.

Obdobně jako je: https://ozrobotics.com/shop/maleetronic-opb9000-reflective-optical-sensor/
https://www.pololu.com/product/2459
https://www.electronics-lab.com/project/reflectance-based-proximity-sensor-using-si1102/

### Reflexive sensor

Od reflexivního snímače na plošném spoji potřebujeme, aby byl citlivý na otvory nebo prohlubně ve 3D vytištěném dílu. Kódovací kotouček by tak neměl vyžadovat žádnou dodatečnou povrchovou úpravu.

Alternativně by snímač měl být citlivý na kódovací pásky vytištěné na papír, nebo fólii.

- [VCNT2020](https://www.vishay.com/optical-sensors/list/product-84285/)
- [OPTOI](https://optoi.com/en/products/components/reflective-sensors)
- [GP2S60](https://eu.mouser.com/datasheet/2/365/gp2s60_e-106.pdf)
- [QRE1113GR](https://eu.mouser.com/datasheet/2/308/QRE1113_D-1814544.pdf)
- [SFH 9206](https://eu.mouser.com/ProductDetail/OSRAM-Opto-Semiconductors/SFH-9206?qs=wWC4CIiyLaOQlR9G3WZMlg==)
- [GP2S700HCP](https://eu.mouser.com/datasheet/2/365/gp2s700hcp_e-800.pdf)
- [EE-SY199](https://eu.mouser.com/datasheet/2/307/EE-SY199-1189542.pdf)
- [OPB733TR](https://eu.mouser.com/datasheet/2/414/OPB733-1545423.pdf)
- [EE-SY1200](https://eu.mouser.com/datasheet/2/307/en-ee_sy1200-24835.pdf)
- [OPR5005](https://eu.mouser.com/datasheet/2/414/OPR5005-1530512.pdf)

#### S integrovaným zpracováním signálu

- [OPB9000](https://cz.mouser.com/ProductDetail/Optek-TT-Electronics/OPB9000?qs=Ok18xCFj7msWl1O2KsmQxQ%3D%3D)

Tenhle snímač vypadá dobře, ale zřejmě se musí alespoň trošku digitálně ovládat. Tím pádem není vhodný pro jednoduché čidlo. Možná by jej někdy v budoucnu bylo dobré využít pro něco jako TFRPM02.

#### Provedení s vývody:

- [OPB715](https://eu.mouser.com/datasheet/2/414/OPB715-716-717-718-1530362.pdf)
- [OPB760](https://eu.mouser.com/datasheet/2/414/OPB760thru763-770thru773-NandT-1545415.pdf)

#### Reflexive encoder

https://eu.mouser.com/datasheet/2/678/av02-2790en_ds_aedr-850x_2016-10-07-1828277.pdf
https://docs.broadcom.com/doc/AV02-0088EN

### Hall magnetic sensor

Magnetický snímač musí být citlivý na magnety zalepené do snímacího kotoučku. Použití magnetického snímače předpokládáme v prostředí, kde hrozí znečištění, které by mohlo ohrozit funkci optického snímače.

- [SL353LT](https://cz.mouser.com/ProductDetail/Honeywell/SL353LT?qs=pB3G9VbQXIenMOyKzoQ33g%3D%3D) - asi není úplně vhodný, protože má push-pull výstup.  Tohle by ale možná šlo vyřešit přidáním tranzistoru

- [AH3572](https://cz.mouser.com/datasheet/2/115/AH3572-1483253.pdf) - má otevřený kolektor, je vhodný pro paralelní spojení s optickým sensorem.

## Zapojení

Modul je potřeba zapojit tak, aby při sepnutí jednoho ze snímačů došlo ke změně polarity výstupního signálu.  Prakticky ale modul bude používán tak, že bude vždy fungovat jen jeden snímač.

ChroustJan, 2020-10-26:
@kaklik neměli by to spíš být dva PCB? Očekávám, že se dopředu bude vědět technologie, která bude použita. Myslím si, že zde potřebujeme mít co nejmenší PCB.

kaklik, 2020-10-26:
> @kaklik neměli by to spíš být dva PCB? Očekávám, že se dopředu bude vědět technologie, která bude použita. Myslím si, že zde potřebujeme mít co nejmenší PCB.

Je to zřejmě možnost.  Podstatné bude hlavně to, jakým způsebem ty PCB budou připevněné a zda budou záménné.

kaklik, 2020-11-12:
Solved by https://github.com/ThunderFly-aerospace/TFPROBE01

Closed 2020-11-12.

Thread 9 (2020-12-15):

Optimalizace rozměru krabičky

kaklik, 2020-12-15:
Krabičku by myslím bylo dobré upravit tak, aby existovala délka šroubu M3, která bude úplně zapuštěna v krabičce a zároveň s jejím použitím půjde vytvořit 3D tisknutelná krabička.

Původní krabička možná počítala se šroubem délky 8mm (Nevím zda to bylo někdy vyzkoušeno).  Takovou délku ale zřejmě nelze použít, neboť v takovém případě nelze středový sloupek podpírající PCB navrhnout tak, aby skrz jeho boky nevznikaly při tisku díry na hranách matice.
Navrhuji proto použít délku šroubu 10mm a matici tak posunout blíže povrchu.  Celkovou tlušťku krabičky je potřeba upravit, tak aby byl ostrý konec šroubu mírně utopený pod stěnou krabičky na protilehlé straně u matice.  Hlava šroubu má zaoblené hrany a může proto mírně vystupovat (např. 0.2mm).

kaklik, 2020-12-21:
Parametry krabičky byly empiricky upraveny tak, aby mohla být stažena šroubem DIN 912 M3x10. Při použití se šroub musí do protilehlé matice zašroubovat pouze lehce.
Silné utažení způsobí deformaci krabičky a přečnívání šroubu z druhé strany.

Closed 2020-12-21.

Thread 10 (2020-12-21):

Change sensor pull-up value to match TFPROBE01

roman-dvorak, 2020-12-21:
Změnit hodnotu pull-upu na vstupu signálu u TFRPM01, tak aby bylo možné TFRPM používat přimo s [TFPROBE01](https://github.com/ThunderFly-aerospace/TFPROBE01)

ChroustJan, 2021-02-11:
Aktuálně se testuje 10k

kaklik, 2021-02-18:
S hodnotou 10k byl při použití v kombinaci [se snímacím bubínkem](https://github.com/ThunderFly-aerospace/TF-G2/issues/64#issuecomment-761890227) pozorován problém, kdy na přímém slunečním světle přestalo fungovat čítání snímače.

Současně existuje předpoklad, že je to způsobeno především prosvícením bubínku slunečním světlem. Je nutné tento problém dále analyzovat. Může však dojít k nutnosti snížit hodnotu pull-upu, aby byla snížena citlivost senzoru.

ChroustJan, 2021-02-18:
Zkusíte tohle nějak analyzovat? Bylo by dobré znát hodnoty do nové várky osazování. A pokud není chtělo by to popsat do návodu, že při použití této technologie může být potřeba doladit hodnoty. Podle zvolené mezery a odrazného materiálu.

kaklik, 2021-02-21:
Tak z aktuálních poznatků vyplývá, že testovaná hodnota pull-upu 4k7 je minimálně pro použití na TF-G2 příliš nízká. Kromě jiného se ukázala i značná citlivost na barvu materiálu. Viz následdující grafy:

Fialová odrazná plocha
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

Modrá odrazná plocha
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

Šedá odrazná plocha
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

V žádném z těchto případů nedocházelo ke spínání vstupu TFRPM a kombinaci pull-up/materiál nelze použít. Při použití rezistoru 10k je situace poněkud lepší:

kaklik, 2021-02-23:
Tady jsou nové obrázky po následujících změnách:

- zvětšení proudu IR LED na 20 mA zmenšením rezistoru R1 ze 180 na 82 Ohm
- Instalace 10k pull-upu na TFRPM in TFPROBE

Fialová
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
Modrá
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
Šedá
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

kaklik, 2021-03-04:
Navrhoval bych  pull-up R1 zkusit používat 22k.   Omezení proudu rezistorem R2 omezit hodnotou 82 Ohm.
Upravit je potřeba i [nastavení hodnot na TFPROBE viz samostatné issue](https://github.com/ThunderFly-aerospace/TFPROBE01/issues/5).

Po těchto úpravách vypadají signály pro fialový a zelený bubínek relativně použitelně.  Systém je ale hodně citlivý na vzdálenost možná zde bude muset dojít ještě k mírným konstrukčním úpravám.

Fialový bubínek:
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

Zelený bubínek ve stejné vzdálenosti jako fialový:
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

Zelený bubínek při kratší vzdálenosti:
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

Šedivý bubínek je ale stále nepoužitelný:

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

ChroustJan, 2021-03-13:
Osazeno R1 22K a R2 82R

kaklik, 2021-03-19:
S nezměněnou konfigurací oproti předchozímu komentáři jsem vyzkoušel bubínek vytištěný z barvy "Teal".

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

Zatím to vypadá, že zhlediska snímání je to nejvhodnější barva.

kaklik, 2021-03-21:
Po úpravě  TFPROBE podle https://github.com/ThunderFly-aerospace/TFPROBE01/issues/5

A při zachování konfigurace TFRPM https://github.com/ThunderFly-aerospace/TFRPM01/issues/10#issuecomment-798528538 , jsem zkoušel změřit napěťový průběh na vstupu TFRPM ze sondy TFPROBE.

### Fialový  klobouček

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

### Teal  klobouček

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

Jak je z grafů vidět, tak hodnota minimálního i maximálního napětí klesla. S tím že maximální napětí je nyní pod hranicí 2V, což neodpovídá vstupním napěťovým úrovním #16 .   Důsledkem toho, je že u barvy Teal je TFRPM senzor část úvratě v "sepnutém stavu" s rozsvícenou LED a nečítá pulzy.

Z testovaných barev  (Šedá, modrá, fialová, Teal, Bílá, Zelená), je teď optimální kotouček vytištěný ze zelené barvy, který funguje spolehlivě.

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

kaklik, 2021-03-23:
Jinak bez kloboučku je na tom výstupu TFPROBE  cca 3V. Což znamená, že v té horní mezi je ještě celkem dost velká rezerva, která zaniká tím že ten senzor je částečně osvětlený odraženým světlem z vnitřku kloboučku.

Pokud by zevnitř bylo něco, co to světlo lépe pohltí, než prázdný prostor, tak by se zřejmě dala snížit ta citlivost na barvu.

kaklik, 2021-08-05:
Záležitost byla nakonec vyřešena přebarvením zubů klobočku viz komentář: https://github.com/ThunderFly-aerospace/TF-G2/issues/64#issuecomment-808915707

Toto přebarvení zřejmě dále umožňuje případně snížit hodnotu pull-upu na TFRPM.

Closed 2021-08-05.

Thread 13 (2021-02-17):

Ověřit správnost I2C adresy na potisku PCB

ChroustJan, 2021-02-17:
Ověřit správnost I2C adresy na potisku PCB. Že platí 0x50 v základním nastavení a 0x51 po přepojení.

kaklik, 2021-02-18:
Zde není moc co kontrolovat, nastavená nula na vstupu A0. Nastavuje adresu na 0x50 viz datasheet.

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

Je akorát podivné, že v PX4 firmware je s adresou 0x50 zacházeno jako s dekadickou adresou 80. Což mi přijde poněkud matoucí.. Dělá se to tak v PX4 běžně? @slimonslimon ?

Každopádně mi ale přijde nepraktické, že propojka nemá označenou adresu, která je zvolena jejím nastavením. Možná to nemusí být nutně přímo v popisku u propojky. Ale měl by tam myslím být odkaz na tabulku z druhé strany, kde je teď však adresa pouze 0x50

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

Myslím že by jako odkaz šla použít ta šipka, kterou symbol letovací propojky na potisku jíž obsahuje.

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

slimonslimon, 2021-02-18:
Těch 80 jsme tam prostě napsal, protože jsem v tom tehdy neviděl moc rozdíl. Žádný specifický důvod v tom není. (původně což možná platí doteď je možné adresu nastavovat parametrem - ten parametr se pak pochopitelně vypisoval dekadicky - celou tuto featuru asi zruším)

ChroustJan, 2021-02-18:
@kaklik důležitý je ten stav ve kterém to je po osazení a budeme to dodávat. Ten kdo do toho zasahuje by měl už něco vědět. Pokud to myslíš tak, že před 0x50 chceš dát symbol toho trojúhelníku tak ok.

Dvě adresy nevím zda tam dávat, aby to nebylo matoucí. A nechce se mi všechny standardně přeškrtávat.

kaklik, 2021-02-18:
> Těch 80 jsme tam prostě napsal, protože jsem v tom tehdy neviděl moc rozdíl. Žádný specifický důvod v tom není. (původně což možná platí doteď je možné adresu nastavovat parametrem - ten parametr se pak pochopitelně vypisoval dekadicky - celou tuto featuru asi zruším)

No to nastavování adresy (nějak) je asi docela důležitý. Protože vzhledem k tomu, že se TFRPM dají řetězit. Tak lidi mají tendenci zapojovat třeba alespoň dva za sebe.  (Už jsme minimálně dotaz na to jestli to jde od jednoho zákazníka měli). Ok ale závěrem zřejmě je, že je celkem zvykem pracovat s dekadickou hodnotou parametrů. Což vede k tomu, aby na PCB byla ideálně vyznačena i dekadická hodnota. Nebo je to zjevné a zákazníci si to převedou? Případně to bude vysvětlené v dokumentaci?  Protože naopak jinde bych rekl, že se s dekadickou formou I²C adresy naopak běžně nepracuje.

slimonslimon, 2021-02-18:
no na PCB bych to uváděl hexadecimálně stradičním 0x na začátku.

ChroustJan, 2021-02-19:
Zkoušel jsem tam dát trojúhelníček a druhou adresu nevypadá to hezky. A nemáme tam moc místa. Navrhuji tam nechat jen 0x50. Pokud si to někdo předělá, tak si to může rozlišit tím, že si tu adresu škrtne. Ty škrtlé nebudou mít 0x50.  Druhá věc je že to chceme prodávat v krabičkách se samolepkou. Napadla mě ta věc, zda ke každé zásilce nedávat samolepku navíc s variantou adresy 0x51. Bylo by to dle návrhu Romana s tím že z výroby by byl křížek u 0x50 a v sáčku by dostali samolepku s křížkem 0x51, pro přelepení. Na každé samolepce by ale byla vždy i druhá adresa aby bylo vidět, že je možné to měnit.

ChroustJan, 2021-02-19:
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

kaklik, 2021-02-20:
Aktuálně vyznačená adresa na modulu 0x50 označuje nastavení z výroby.

Jako alternativní možnost vidím umístění adres nad GND pin hřebínku.
Dokumentaci v readme jsem ale upravil tak, aby odpovídala stavu prezentovanému v komentáři výše.  https://github.com/ThunderFly-aerospace/TFRPM01/issues/13#issuecomment-781923042

Closed 2021-02-20.

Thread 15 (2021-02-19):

Proražená dioda D1

kaklik, 2021-02-19:
Na jednom z modulů došlo během relativně běžného používání k proražení zenerovo diody D1.  Hlavní anomálií byla nízká teplota (okolo -12 °C).

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

Lze předpokládat, že dioda odešla v důsledku otevření na vyšším napětí s následným nadproudem, který diodu zničil.
Podle schéma je tam neznámý typ diody s otevíracím napětím 5.6V To je však velmi blízko změřenému napájecímu napětí 5.4 V při napájení z akumulátoru přes CUAV power modul.
Vzhledem k absenci přesného označení typu diody ve schéma, nelze určit jaká je její teplotní charakteristika a zda na této události mohla mít podíl nízká teplota během provozu.

ChroustJan, 2021-02-21:
@kaklik  BZV55C-5,6V

kaklik, 2021-03-04:
K tomuto problému bylo vytvořeno [issue v oficiální dokumentaci Pixhawk.](https://github.com/pixhawk/Pixhawk-Standards/issues/15#issuecomment-786302167)
Zůstává však bez relevantního řešení.

kaklik, 2021-03-06:
Issue v dokumentaci stále zůstává bez odpovědi. Navrhuji problém zkusit vyřešit použitím typu zenerovo diody s vyšším otevíracím napětím: BZV55C 6.2BSA

ChroustJan, 2021-03-07:
@kaklik  myslíš prostě BZV55C6V2 ? Nenašel jsem co znamená BSA

kaklik, 2021-03-07:
> @kaklik myslíš prostě BZV55C6V2 ? Nenašel jsem co znamená BSA

BSA specifikuje možný rozptyl otevíracího napětí. Viz datasheet například zde: https://www.rectron.com/data_sheets/bzv55c-bs.pdf

ChroustJan, 2021-03-12:
Parametr je to hezký, ale našel jsi místo, kde to jde koupit?

Máme tuto: https://www.tme.eu/cz/details/bzv55c6v2/zenerovy-diody-smd/dc-components/

ChroustJan, 2021-03-13:
Dán tento typ:  https://www.tme.eu/cz/details/bzv55c6v2/zenerovy-diody-smd/dc-components/

Closed 2021-03-21.

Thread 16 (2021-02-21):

Vstupní logické úrovně

kaklik, 2021-02-21:
Snažil jsem se teď zjistit, jaké jsou skutečné hodnoty vstupních napěťových úrovní na vstupu IN sondy.
Zjistil jsem, že to vlastně není vůbec snadné, neboť ve schéma není jasné, na jaké napájecí napětí je připojen smittuv klopný obvod.

Teprve až po otveření kicadu lze zjistit, že je trvale připojen na 3.3V.

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

Nicméně i to úplně neřeší situaci, neboť v [datasheetu](https://assets.nexperia.com/documents/data-sheet/74HC_HCT1G14.pdf) je asi opomenuta tabulka úrovní pro hodnotu napájení 3.3V.

I tak je ale rozptyl rozhodovacích úrovní, pro mne nečekaně velký. Obávám se tak, zda z použití této součástky nemohou v budoucnu vzniknout nějaké potíže. Například ve smyslu, že mezi jednotlivými kusy by bylo potřeba mít různé hodnoty pull-up rezistorů

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

Zatím ale praktické zkušenosti tomuto rizikovému scénáři příliš nenasvědčují. Nicméně je zřejmě potřeba provést testy na více různých kusech, ideálně i z různých sérií.

Nyní jsem se pokusil alespoň zviditelnit napájecí nožičku na schématické značce ve schéma. Nicméně jsem si pak všiml, že v repozitáři zřejmě není nahraný poslední návrh. Tím pádem jsem tyto změny neuložil.

ChroustJan, 2021-02-22:
Napájecí napětí je definováno zde:
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

kaklik, 2021-02-23:
Na základě #17 navrhuji přejít na obvod [5SN74LVC1G14-Q1](https://www.ti.com/lit/ds/symlink/sn74lvc1g14-q1.pdf), který logické úrovně definuje o něco přesněji.

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

kaklik, 2021-02-25:
Pro praktické účely bych nyní navrhoval pracovat s předpokladem, že potřebujeme dosáhnout napěťových úrovní pod 0.58 V pro log 0 a  více jak 2V pro log 1.

Další pokračování bude v issue #10

Closed 2021-02-25.

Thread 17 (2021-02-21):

Zatížení 74HC1G14GW proudem z LED

kaklik, 2021-02-21:
Při řešení  #16 jsem zjistil, že v [datasheetu](https://www.ti.com/lit/ds/symlink/sn74hc14.pdf?ts=1613907697872) se zmiňují o:
"Recommended output conditions: –  Load currents should not exceed 4 mA per output"

Přibližným odhadem (3,3−1,7)÷180  jsem ale zjistil, že proud skrz LED je nyní zřejmě něco jako  0,0089A. Což zřejmě nesplňuje tento požadavek.

Je tak na zvážení, zda není vhodné použít jiný typ této součástky.

ChroustJan, 2021-02-22:
@kaklik zkusil by jsi prosím co nejdříve najít vhodnou náhradu?

kaklik, 2021-02-22:
> @kaklik zkusil by jsi prosím co nejdříve najít vhodnou náhradu?

Pracuju na tom. Domnívám se ale, že by bylo zároveň vhodné zjistit, jak moc se sníží jas indikační LED v případě, že se dodrží výše uvedené kritérium zátěže výstupu.

kaklik, 2021-02-23:
Asi bych navrhova začít používat tohle: [SN74LVC1G14-Q1](https://www.ti.com/lit/ds/symlink/sn74lvc1g14-q1.pdf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)

Je to sice hůře dostupné a mírně dražší, ale není to takový mizerný řešení, jako ten předchozí typ.
Tohle je navíc kvalifikovaný pro automotive a má to vysokou ESD odolnost.

ChroustJan, 2021-02-23:
Vypadá to dobře. Pokud by se chtělo šetřit, tak je ke zvážení verze bez Q1. Ale myslím si, že příplatek 1kč si můžeme dovolit.

ChroustJan, 2021-03-13:
V novém osazování použito IO: SN74LVC1G14-Q1

kaklik, 2021-03-21:
Změřil jsem napěťové úrovně na  výstupu IO U2A a na LED.

### Průběh napětí na výstupu IO

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

### Průběh napětí na LED D2

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

Z obou průběhů je vidět, že úbytek na rezistoru R4 s hodnotou 51 Ohm, je

Closed 2021-03-21.

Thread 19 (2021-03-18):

Tolerance výšky sloupku pod PCB

kaklik, 2021-03-18:
Aktuální krabička má zřejmě příliš vysoký sloupek pod PCB, což způsobuje, že se krabička nedá úplně uzavřít.

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

Když jsem sloupek trochu ubral vrtákem, tak se krabička už dovře. Jen toto ubrání sloupku je nepřesné, takže se vlivem prohnutí víčka krabička neuzavře všude.
Je však možné, že obdobný problém je i s ploškami, který podpírají PCB na straně u hřebínkového konektoru.

Krabička na obrázku je totiž mírně anomální a byla vytištěna s tloušťkou vrstvy 0.2mm na rozdíl od původních 0.1mm, jako předchozí verze.

kaklik, 2021-03-19:
Vidím, že je teď ten sloupek ubraný celkem hodně.

https://github.com/ThunderFly-aerospace/processor3D/issues

Nevím jestli to není až moc konzervativní. Očekával jsem toleranci tak 0.5mm

kaklik, 2021-03-19:
Vyřešeno, krabička lze nyní zavřít.   Otestováno s TFRPM01B.

Closed 2021-03-19.

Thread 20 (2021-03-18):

Svítivost LED pod samolepkou

kaklik, 2021-03-18:
Aktuální samolepka je natištěna na bílé PVC fólii.  Indikační LED skrz fólii nesvítí příliš zřetelně:

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

Na samolepce je navíc vidět, že nesvítí celá bílá plocha vlivem posunutí samolepky při lepení na krabičku.  Tmavá plocha okolo puntíku ale naopak prosvětlená není, čemuž pomáhá černý lem okolo bílého puntíku.

Možná řešení
-  [x] Zvětšit proud LED, aby bylo dosaženo maximální svítivosti  #17
-  [x] Zvětšit otvor pod samolepkou nad průměr puntíku na samolepce -  tím bude navíc zvětšena tolerance k nepřesnému lepení
-  [x] Otvor směrem k LED udělat kónický s průměrem mírně větším, než je průměr otvoru PCB pro LED
-  [x] Ztenčit víčko, aby LED byla blíže samolepce
-  [ ] Samolepku objednat na průhledné fólii

ChroustJan, 2021-03-18:
Za mě to buď neřešit, nebo udělat úpravu krabičky.

ChroustJan, 2021-03-19:
Bude zvýšen proud LED na 24mA. R4 ze 180R bude 51R.

kaklik, 2021-03-20:
Ještě mne napadla jedna možnost, jak to zlepšit - snížit tloušťku víčka. Nyní je konec šroubu při dotažení utopený o 1,45mm pod povrchem krabičky.  Je zde tak 1mm rezerva na přiblížení LED k samolepce.

roman-dvorak, 2021-03-20:
Dobře, snížím tloušťku víčka o 1mm (pokud tomu něco nebude vadit).

Na fotce z prvního komentáře jsem vůbec netušil, že ta dioda svítí. Nová fotka je už s úpravou, kdy do led teče vyšší proud?

Moc se mi nelíbí, jak to svítí i mimo kroužku. Navrhoval bych ho zase trochu zúžit a nechat kuželovitý.

Myslím, že tato úprava neblokuje focení aktuální verze.

kaklik, 2021-03-20:
> Na fotce z prvního komentáře jsem vůbec netušil, že ta dioda svítí. Nová fotka je už s úpravou, kdy do led teče vyšší proud?
>

Ne, to je zatím se starým PCB TFRPM01B. Stejný proud, jako předchozí fotka.

> Moc se mi nelíbí, jak to svítí i mimo kroužku. Navrhoval bych ho zase trochu zúžit a nechat kuželovitý.
>

Ok, jak myslíš, mě tohle zrovna nijak nevadí.

kaklik, 2021-03-23:
> Dobře, snížím tloušťku víčka o 1mm (pokud tomu něco nebude vadit).

Tohle je zřejmě vhodné udělat i kvůli montáži. Tu normální nerezovou matku se mi před chvílí pod tou samolepkou podařilo skřížit, což je docela nepříjemná situace.  Předpokládám, že nižší díra tomu alespoň trochu zabrání.

roman-dvorak, 2021-03-24:
Víčko ztenčeno o 1 mm v #1519754

kaklik, 2021-03-24:
Pro svítivost LED jsme udělali maximum. Aktuální stav je použitelný. Pro ty, co vyžadují ještě větší svítivost jsem založil[ tenhle návod](https://github.com/ThunderFly-aerospace/TFRPM01/blob/TFRPM01C/doc/README.md).

Closed 2021-03-24.

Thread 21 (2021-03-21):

Precise positioning of the Pulse LED

kaklik, 2021-03-21:
Při testování svítivosti LED #20  jsem přišel na to, že otvor v krabičce zřejmě není přesně na správném místě odpovídajícím otvoru v PCB pro LED.
Tahle skutečnost, pokud se potvrdí, tak kromě krabičky ovlivňuje ještě i návrh samolepky #14.

roman-dvorak, 2021-03-24:
Ano, vypadá to tak, že je LED skutečně posunutá.

Takto vypadá posuv na PCB oproti šroubu.
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

Na krabičce/samolepce je to oproti šroubu na druhé straně. (zjistím přesnou hodnotu)

Tohle bych navrhoval vyřešit posunutím LED na PCB při další výrobě. V okolí LED je relativně místo a připadá mi to jako bezpečná úprava. (Pokud jsou aktuální samolepky vyhovující)

kaklik, 2021-03-24:
Jo souhlasím..  jen tu prosím pak napiš, kam @ChroustJan  má tu LED posunout. Nebo případně, jestli je ten screenshot správně, tak to zřejmě jde rovnou udělat.

roman-dvorak, 2021-03-24:
Ne! ještě to @ChroustJan  nedělej, pošlu přesné umístění.

kaklik, 2021-03-24:
@roman-dvorak  Není náhodou možné, že puntík na samolepce je správně, ale je špatně díra v krabičce?
Protože je mi podezřelé, že už se mi po několikáté podařilo tu samolepku vůči puntíku pro LED nalepit posunutou na stejnou stranu..

roman-dvorak, 2022-03-17:
Na PCB byla LEDka posunutá na druhou stranu, než měla být. Byla posunuta o přesnou pozici, která vychází z openscadu, ale na druhou stranu. To vytvořilo posuv o více než půl milimetru oproti otvoru.  Kontroloval jsem, že to sedí s openscadem i se svg samolepky.

Zároveň jsem tam změnil footprint pro LEDku z knihoven z Kicadu - mělo by to usnadnit osazování.

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

Opraveno ve verzi D

ChroustJan, 2022-03-21:
@roman-dvorak přijde mi, že naše LED do zvoleného pouzdra nepasuje :(
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

ChroustJan, 2022-07-20:
Provedl jsem opravu pouzdra LED, ale bohužel jsem posunul pozici LED. Je potřeba ohlídat správnou pozici. @roman-dvorak není možný nějaký posun, když bude docházet k tisku nových samolepek a výrobě nové krabičky?

kaklik, 2022-09-28:
Tohle je teď v jakém stavu? Je to v nové revizi D už vyřešené, nebo není?

ChroustJan, 2022-09-29:
Pro verzi D jsem navrhl nové frézované pouzdro. Pozice jsou nové po dohodě s @roman-dvorak.

roman-dvorak, 2022-09-29:
Jo, vzhledem k tomu, že tam ledky budou dvě, bude úprava v krabičce a
samolepce, tak tohle nemá smysl řešit.

Nové pozice jsou umístěny tak, že je lze snadno odměřit od středu šroubu.

Dne čt 29. 9. 2022 11:31 uživatel jacho ***@***.***> napsal:

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

Closed 2022-09-29.

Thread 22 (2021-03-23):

Update of the photos

kaklik, 2021-03-23:
- [ ]  Add red case color option
- [ ]  Correct cable orientation and [color-coding of hall-probe](https://cdn.tindiemedia.com/images/resize/qaB5V-p6I7LfV0J9gSIOM_i0yxk=/p/full-fit-in/1200x800/i/085591/products/2021-03-22T21%3A41%3A37.424Z-TFRPM01_magnetic_probe.j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).

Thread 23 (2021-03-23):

Kolize R1 s hranou krabičky

kaklik, 2021-03-23:
Díky změně rozložení součastek, rezistor R1 koliduje s podpěrou PCB v krabičče.
Řešením zřejmě je podpěrnou část po stranách hřebínku J1 trochu zkrátit, aby na R1 vzniklo místo.

roman-dvorak, 2021-03-24:
#1519754 kolizní hrana pousunuta směrem ven z krabičky o 2 mm

kaklik, 2021-03-24:
Vyřešeno, PCB nyní do krabičky pasuje bez kolize s rezistorem.

Closed 2021-03-24.

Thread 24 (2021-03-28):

Dimensions

kaklik, 2021-03-28:
Chtěl jsem ověřit jak lze vytvořit výkres ve FreeCADu a při té příležitosti jsem zjistil, že v souboru [TFRPM01C.wrl](https://github.com/ThunderFly-aerospace/TFRPM01/blob/TFRPM01C/hw/sch_pcb/TFRPM01C.wrl) jsou špatná data.

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

ChroustJan, 2021-03-29:
Nedalo by se tohle generovat nějak automaticky? Aktuálně jsem nějak rychle nepřišel nato, jak to vygenerovat nově.

kaklik, 2021-03-29:
> Nedalo by se tohle generovat nějak automaticky? Aktuálně jsem nějak rychle nepřišel nato, jak to vygenerovat nově.

Je to jeden z formátů, který lze ručně importovat z KiCAD PCB prohlížeče. Jestli to jde exportovat nějak automaticky je zřejmě spíše otázka na @roman-dvorak .

roman-dvorak, 2021-03-29:
Do doby, kdy se používal starý formát, tak bych řekl docela jistě ano :) Ale teď na to neumím odpovědět. Je potřeba zjistit chyby, co tam aktuálně jsou. I tohle generování se nyní provádí nějak jinak.

ChroustJan, 2021-03-29:
Tohle mi přijde vhodné generovat automaticky, protože na aktualizaci se dá snadno zapomenout. Dává mi dost zabrat udržet schéma aktuální.

ChroustJan, 2021-08-25:
Vygenerování nového modelu:
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

Closed 2021-08-25.

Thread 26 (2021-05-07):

Header pinout in top silksceen layer

roman-dvorak, 2021-05-07:
pinout hřebínku pro připojení sondy je jen z jedné strany PCB, pokud je namontovaný popiskem dolu (bez krabičky) tak není popisek čitelný. Při další vyrobě bych navrhoval přidat pinout do horní vrstvy silkscreenu (tam, kde jsou součástky)

roman-dvorak, 2022-03-17:
Ve verzi D jsou popisky pinů přidány i pod hřebinek

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

kaklik, 2022-09-28:
Myslím, že provedení popisů je v pořádku, takže se může zavřít.

Closed 2022-09-28.

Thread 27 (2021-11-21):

Optical probe readout

laronll, 2021-11-21:
I would like to know if the optical probe needs to have any code change for it to work? Another question is that aiming the board perpendicular to a propeller with attached reflective material should make the sensor get readings? And if I am looking for RPM readings I should be looking for the frequency( or count, etc) that the code prints out?

Thank you in advance

roman-dvorak, 2021-11-21:
Hi, I assume that you want to use it with autopilot with PX4 firmware?

There should be nothing to modify anything. The SW should be ready for such a measurement. Number of reflective marks (per 1 rotation) can be set through [PX4 parameters](http://docs.px4.io/master/en/advanced_config/parameter_reference.html#PCF8583_ADDR). The driver provides value as frequency (count of revolutions per second, in Hz). Frequency is logged by autopilot and forwarded through MavLink network.

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

In addition to the sensor (frequency sensor) TFRPM01, we also have a probe [TFPROBE02](https://github.com/ThunderFly-aerospace/TFPROBE01) (on the picture) that contains the optical reflective sensor itself. The sensor used works at a small distance (units of mm) so I think it is better to measure the engine speed than the propeller. (The reflective material on the propeller can change the position of the centre of gravity quite significantly.) Or create your custom probe that will detect reflections from the propeller at a bigger distance. The TFRPM on the input contains a pullup resistor.

roman-dvorak, 2022-03-17:
@laronll  Do you have any additional questions? Otherwise, I would close this issue.

Closed 2022-09-19.

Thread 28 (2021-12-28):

Power  LED

roman-dvorak, 2021-12-28:
Modulu chybí ledky signalizující napájení a signál z INT pinu.

Na INT signálu je například poznat, jestli IO je zinicializovaný nebo by přes něj šlo blikat po načtení několika vstupních signálů tak, aby to bylo viditelné okem i při provozních otáčkách rotoru.

roman-dvorak, 2022-03-17:
Interrupt ledka při neinicializaci nebude blikat (jak bylo zamýšleno), protože nemá zdroj hodin. Takže totu LEDku bych tam v dalšich verzích nedával.

Je potřeba se rozhodnout, jestli nepřidat power LEDku.

kaklik, 2022-03-17:
> Interrupt ledka při neinicializaci nebude blikat (jak bylo zamýšleno), protože nemá zdroj hodin. Takže totu LEDku bych tam v dalšich verzích nedával.

A jde s ní blikat aspoň softwarem, nebo ten INT signál nelze vůbec ovládat přes I2C?

> Je potřeba se rozhodnout, jestli nepřidat power LEDku.

Za mě je to dobrý nápad, pokud to technicky lze a nezvětší nároky na PCB. Nemusí ale být reverse mount.

kaklik, 2022-09-28:
Zdá se že ve schéma TFRPM01D je tato LED implementována ve formě zelené reverse mount LED. Chybí u ní však hodnota rezistoru. Není tak jasné, jak moc bude v konečném provedení svítit.

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

Closed 2023-02-08.

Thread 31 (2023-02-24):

Update sticker

kaklik, 2023-02-24:
Add the OSHWA registration number:
https://github.com/oshwa/certification-mark

kaklik, 2023-04-23:
Celé označení CZ000009 se na nálepku nevejde.

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

Bude tam tak, alespoň OSHW logo.

Closed 2023-04-23.

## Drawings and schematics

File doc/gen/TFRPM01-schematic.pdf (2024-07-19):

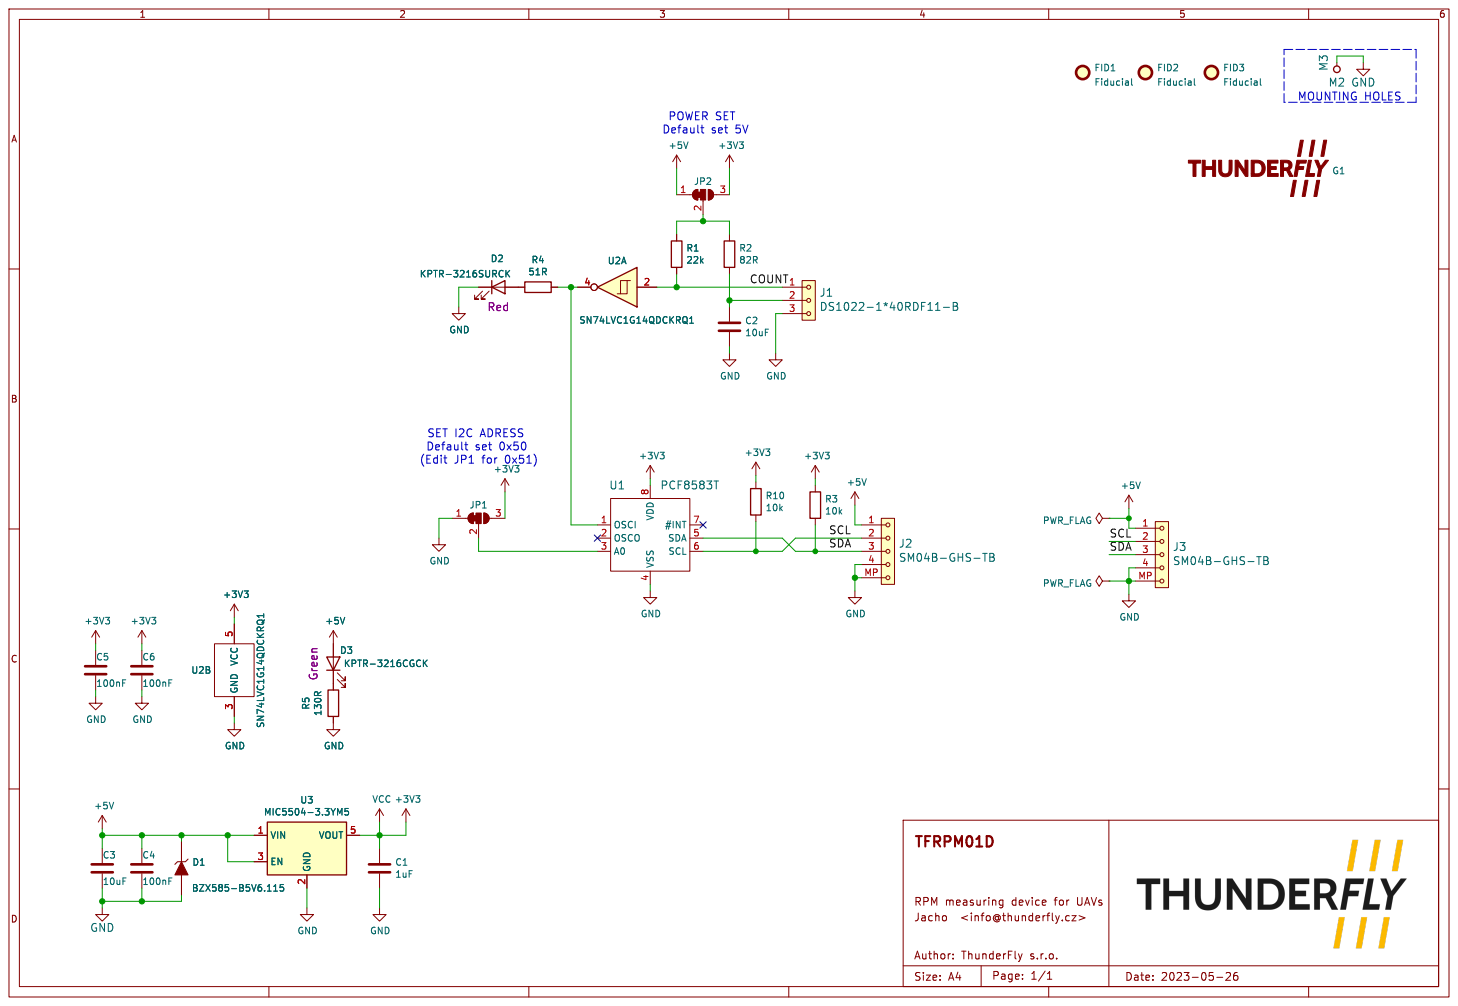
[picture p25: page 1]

2 EN 3 VOUT 5 R5 130R GND GND

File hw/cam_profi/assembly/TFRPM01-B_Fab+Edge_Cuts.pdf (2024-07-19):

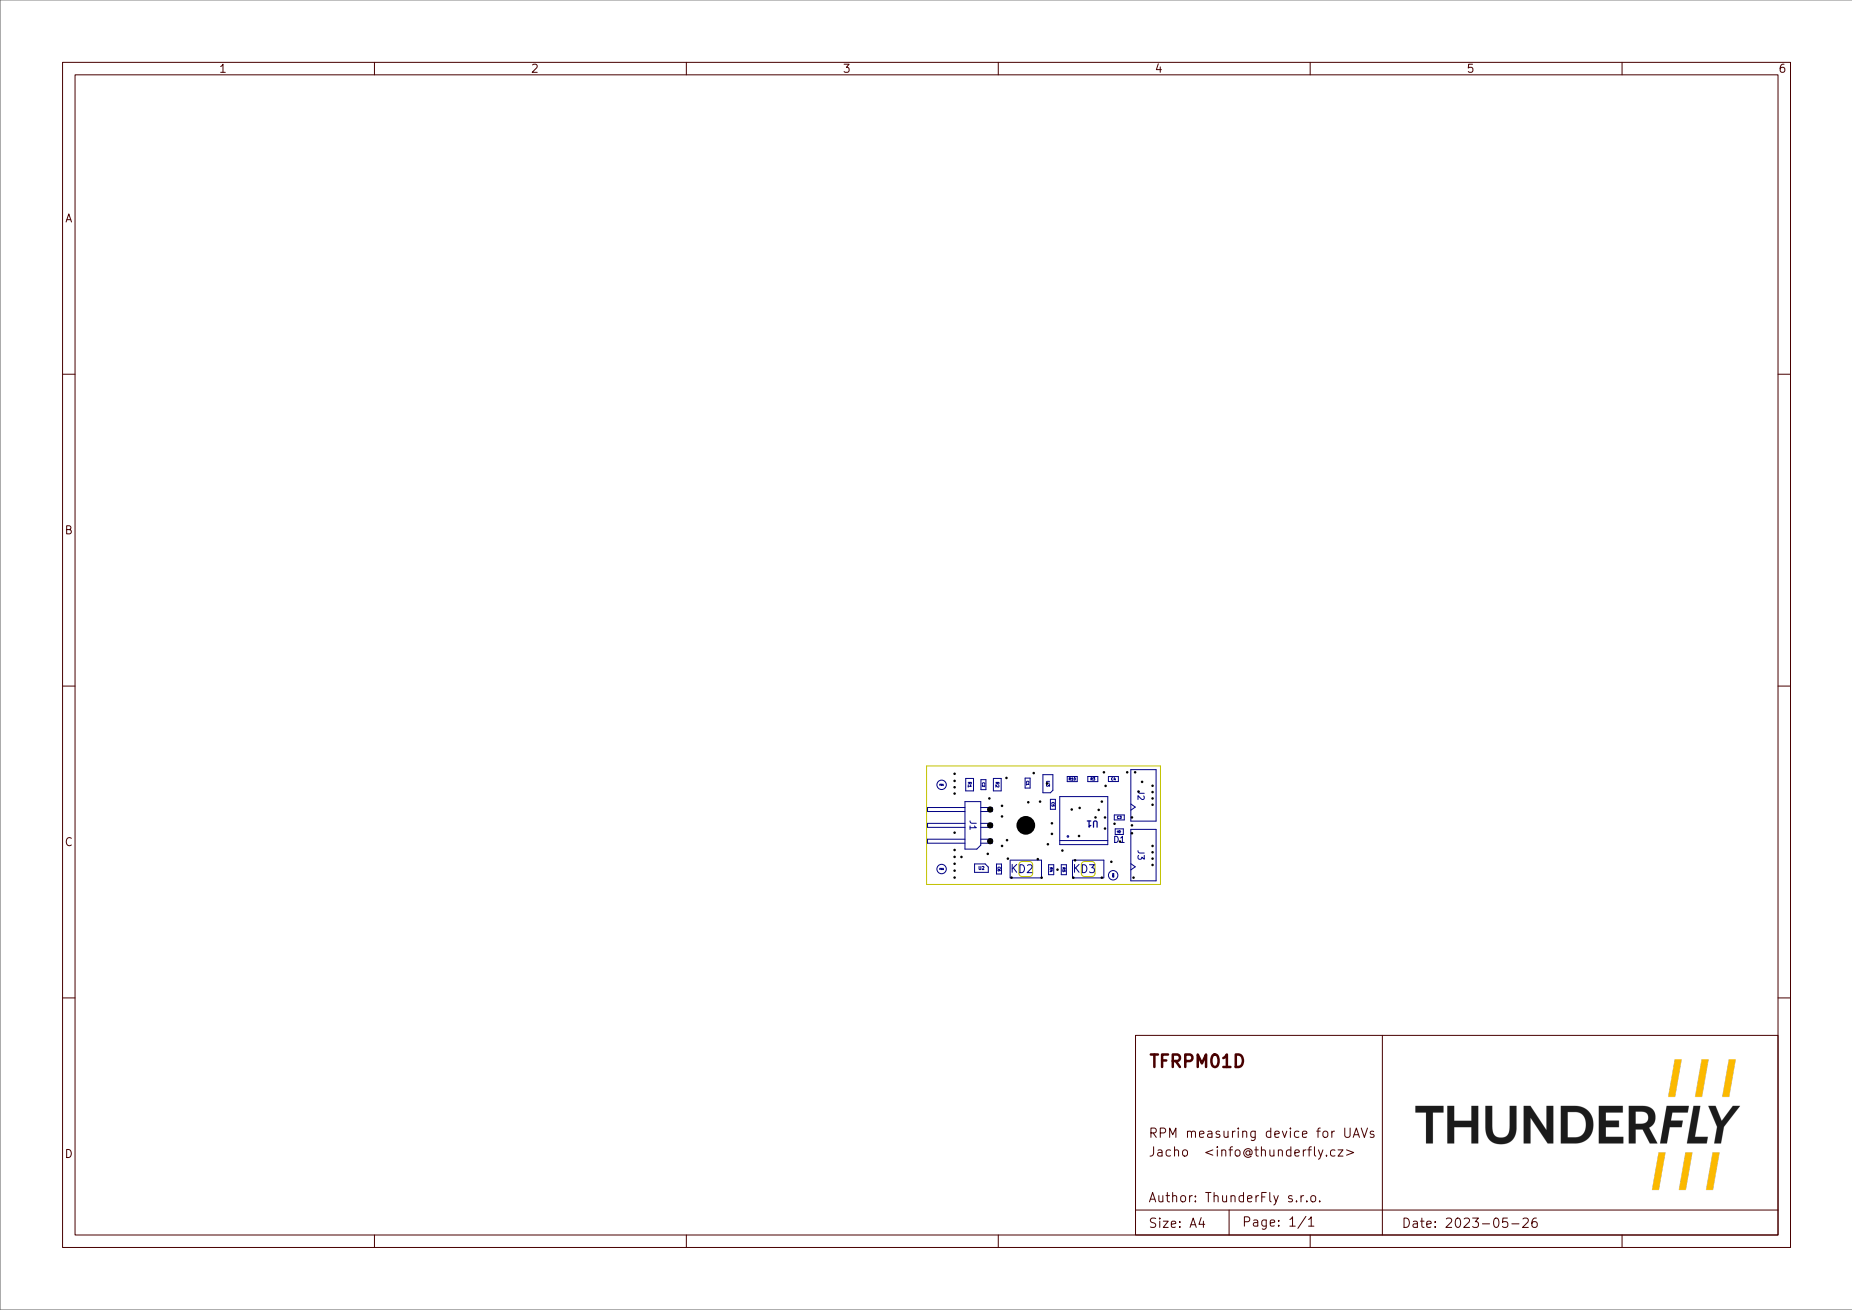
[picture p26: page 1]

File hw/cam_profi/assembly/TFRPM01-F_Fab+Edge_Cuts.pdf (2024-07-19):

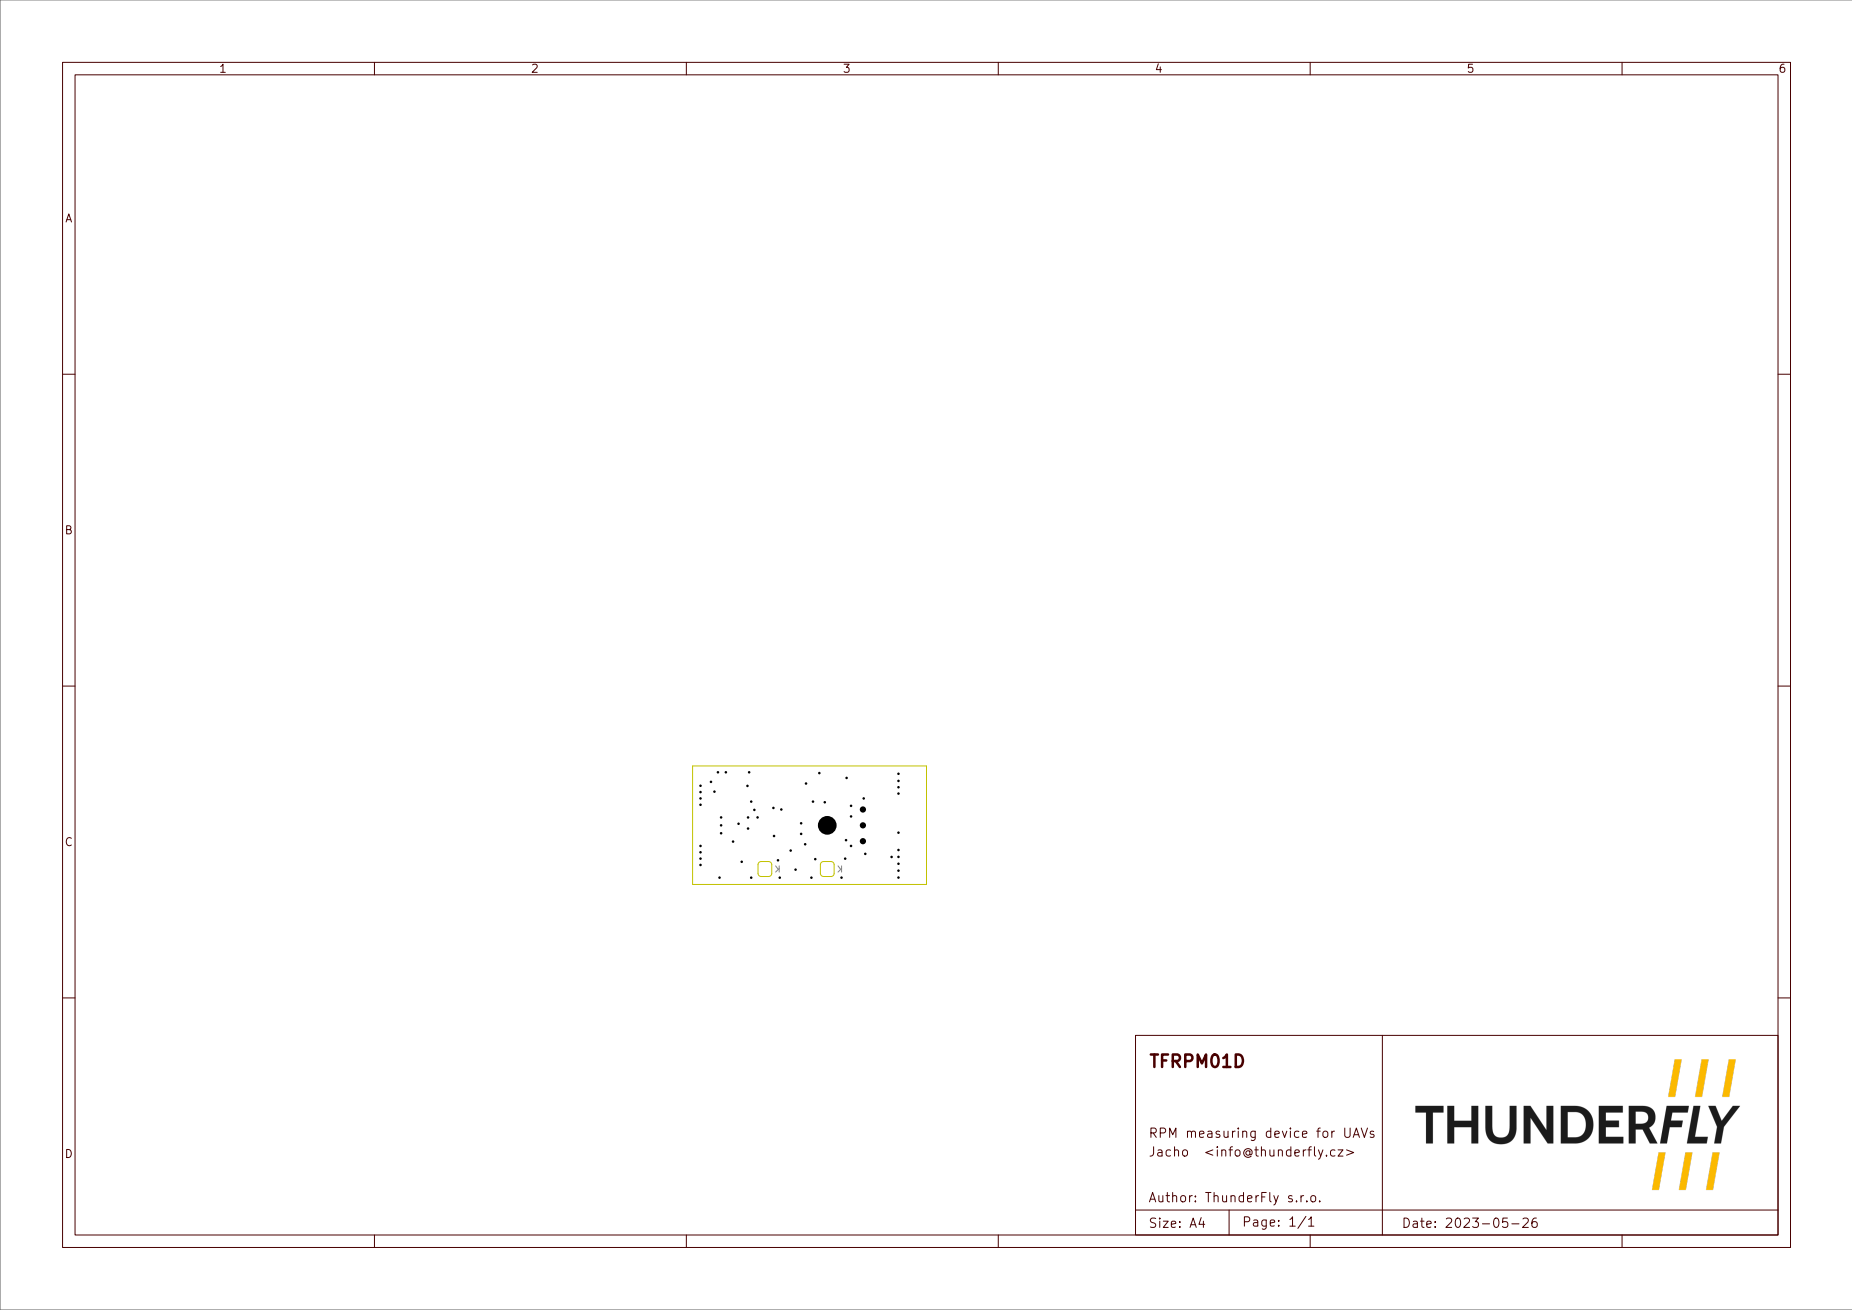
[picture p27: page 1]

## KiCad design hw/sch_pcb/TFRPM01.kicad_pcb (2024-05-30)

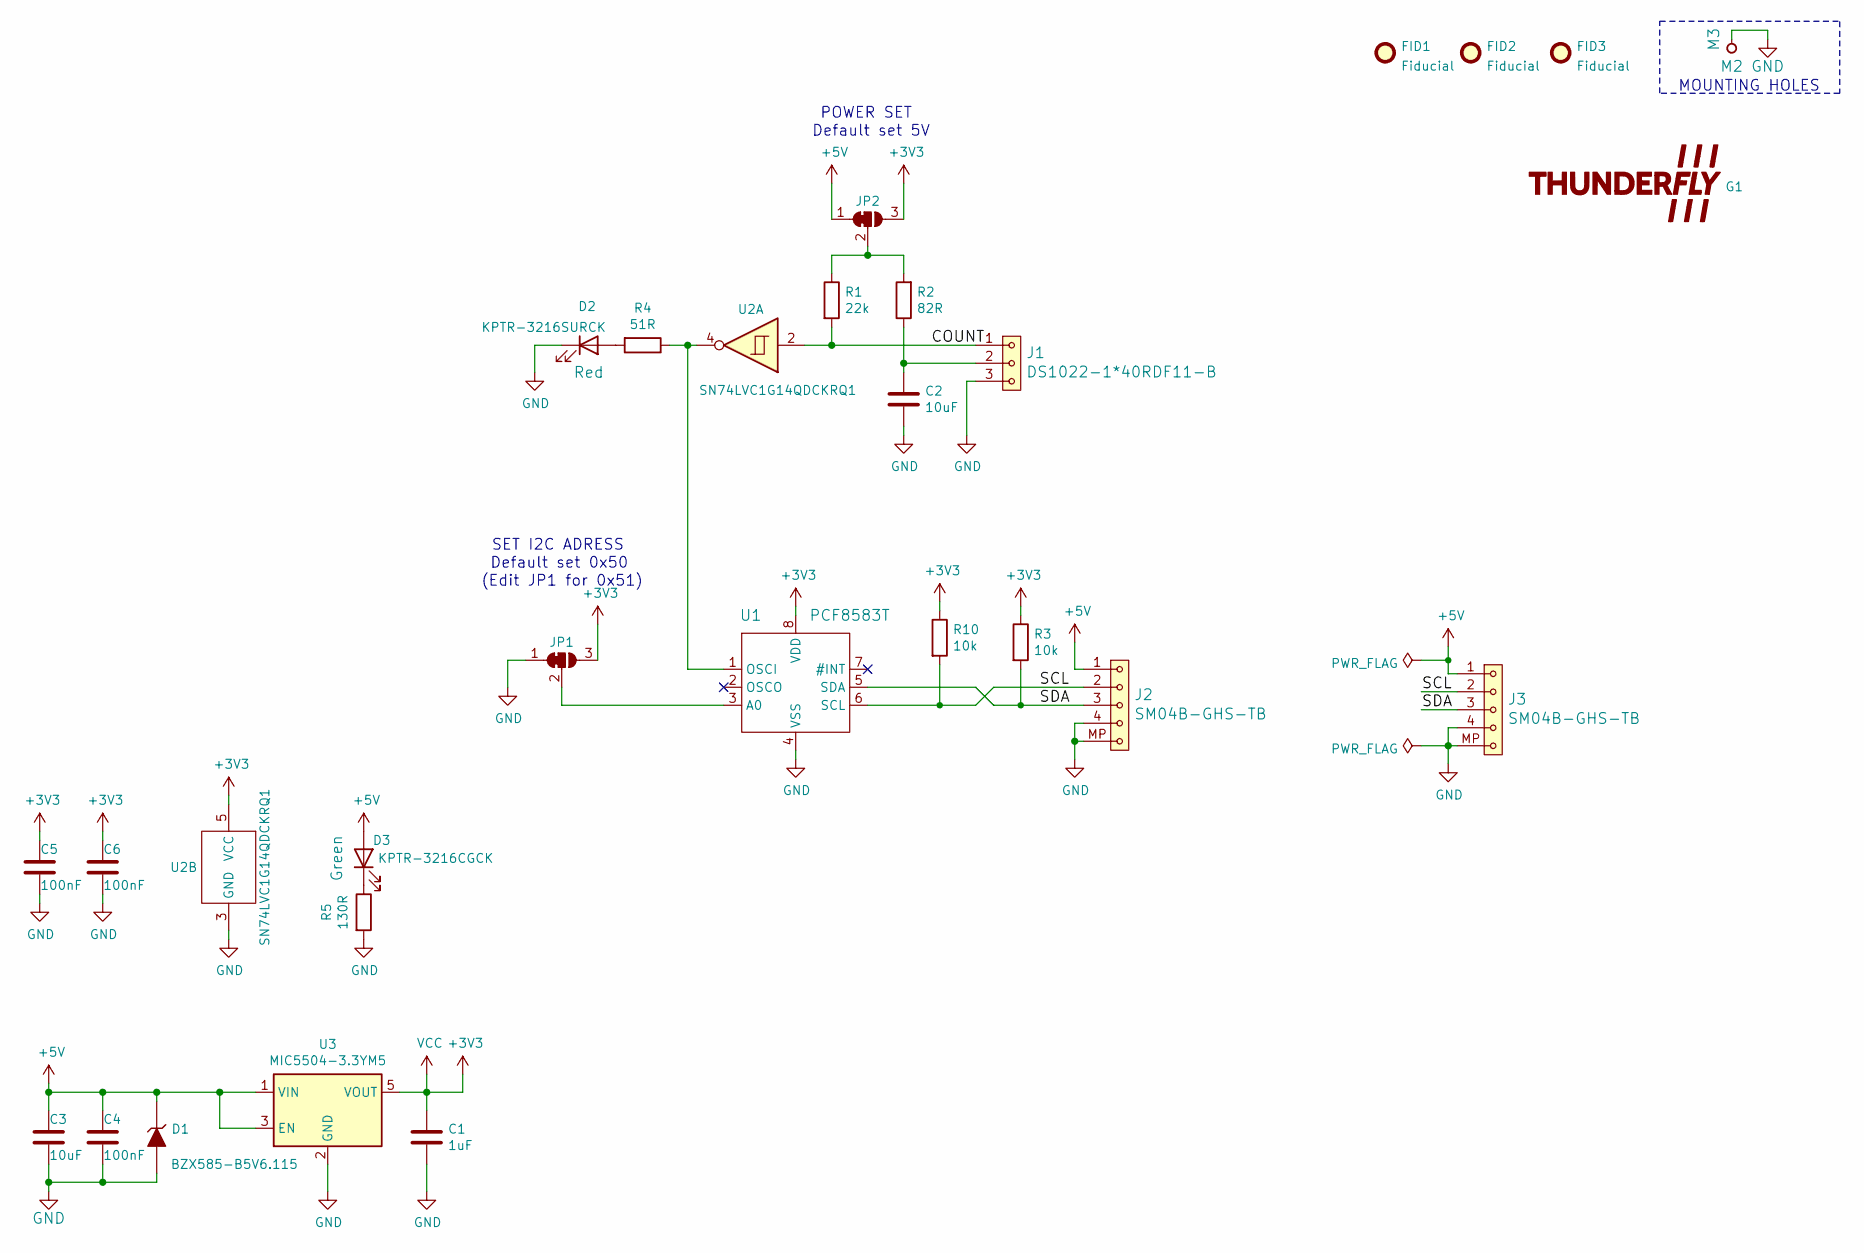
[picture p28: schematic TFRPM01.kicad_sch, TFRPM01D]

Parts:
C1: 1uF; C_0603_1608Metric
C2, C3: 10uF; C_0603_1608Metric
C4, C5, C6: 100nF; C_0603_1608Metric
D1: BZX585-B5V6.115; D_SOD-523
D2: KPTR-3216SURCK; LED_1206_2
D3: KPTR-3216CGCK; LED_1206_2
FID1, FID2, FID3: Fiducial; Fiducial_0.5mm_Mask1.5mm
G1: LOGO; TF
J1: DS1022-1*40RDF11-B; PinHeader_1x03_P2.54mm_Horizontal
J2, J3: SM04B-GHS-TB; JST_GH_SM04B-GHS-TB_1x04-1MP_P1.25mm_Horizontal
JP1, JP2: SolderJumper_3_Bridged12; SolderJumper-3_P1.3mm_Bridged12_RoundedPad1.0x1.5mm
M2: M3; MountingHole_3mm
R1: 22k; R_0805_2012Metric
R2: 82R; R_0805_2012Metric
R3, R10: 10k; R_0603_1608Metric
R4: 51R; R_0603_1608Metric
R5: 130R; R_0603_1608Metric
U1: PCF8583T; SOT176-1
U2: SN74LVC1G14QDCKRQ1; SOT-353_SC-70-5
U3: MIC5504-3.3YM5; SOT-23-5

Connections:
+3V3: C1.1, C5.1, C6.1, JP1.3 (B), JP2.3 (B), R3.1, R10.1, U1.8 (VDD), U2.5 (VCC), U3.5 (VOUT)
+5V: C3.1, C4.1, D1.1 (K), D3.2 (A), J2.1, J3.1, JP2.1 (A), U3.1 (VIN), U3.3 (EN)
/COUNT: J1.1, R1.2, U2.2
/SCL: J2.2, J3.2, R10.2, U1.6 (SCL)
/SDA: J2.3, J3.3, R3.2, U1.5 (SDA)
GND: C1.2, C2.2, C3.2, C4.2, C5.2, C6.2, D1.2 (A), D2.1 (K), J1.3, J2.4, J2.MP, J3.4, J3.MP, JP1.1 (A), M2.1, R5.2, U1.4 (VSS), U2.3 (GND), U3.2 (GND)
unnamed: C2.1, J1.2, R2.1
unnamed: D2.2 (A), R4.2
unnamed: D3.1 (K), R5.1
unnamed: JP1.2 (C), U1.3 (A0)
unnamed: JP2.2 (C), R1.1, R2.2
unnamed: R4.1, U1.1 (OSCI), U2.4

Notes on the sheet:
Default set 5V
(Edit JP1 for 0x51)
MOUNTING HOLES
Default set 0x50
POWER SET
SET I2C ADRESS

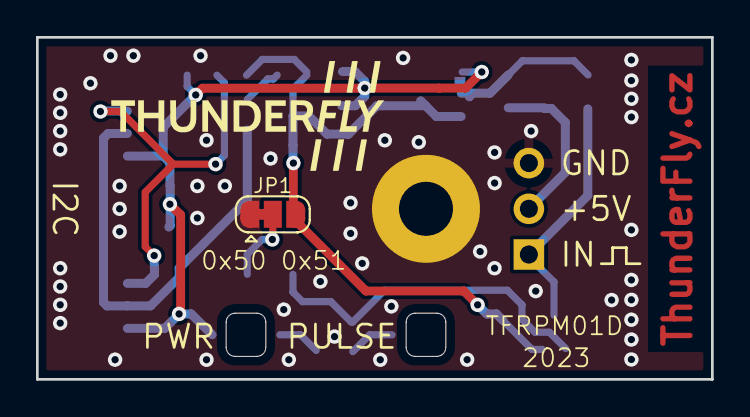
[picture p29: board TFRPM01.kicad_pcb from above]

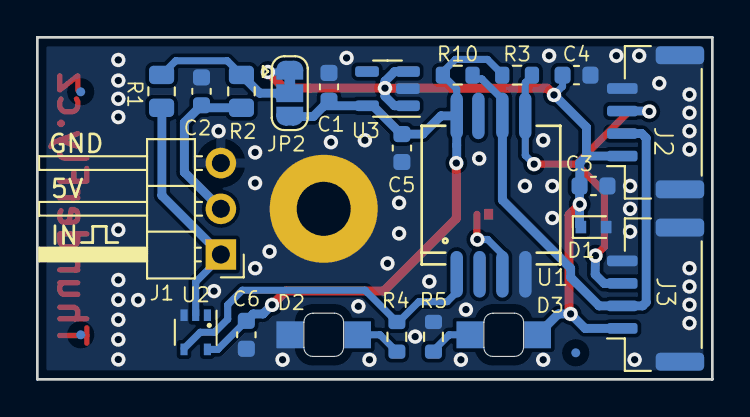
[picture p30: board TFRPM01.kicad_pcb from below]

Board: 2 copper layers, 37.5 x 19.0 mm, 28 parts (26 on the bottom side), 12 nets.

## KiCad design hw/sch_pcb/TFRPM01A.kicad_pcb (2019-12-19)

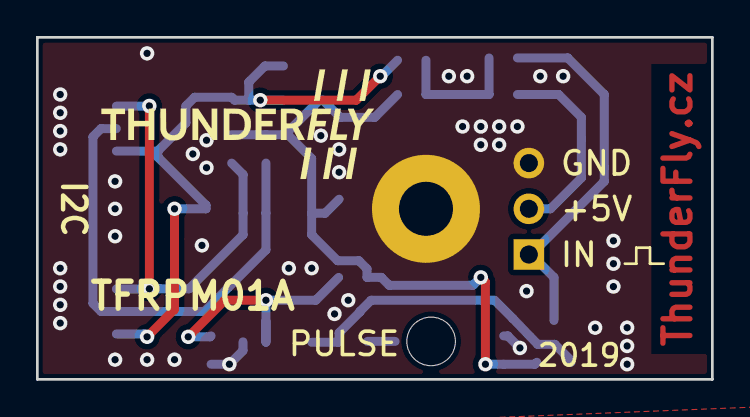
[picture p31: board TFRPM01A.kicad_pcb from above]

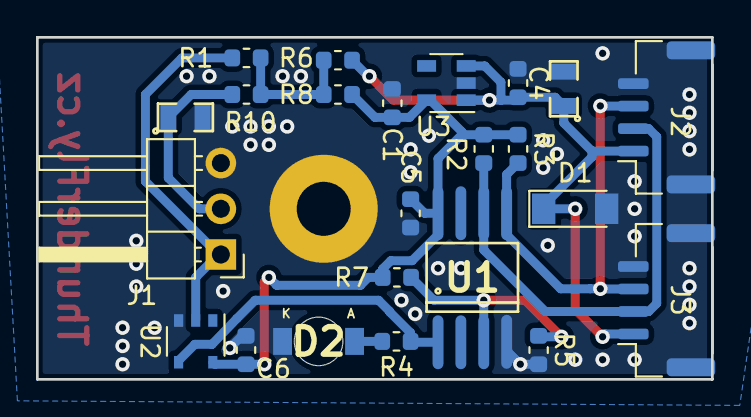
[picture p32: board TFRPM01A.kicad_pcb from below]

Board: 2 copper layers, 37.5 x 19.0 mm, 24 parts (24 on the bottom side), 11 nets.

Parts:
C1: 1uF; SMD-0603
C2, C3: 10uF; SMD-0805
C4, C5, C6: 100nF; SMD-0603
D1: ZENER-5.6V; Diode-MiniMELF_Standard
D2: LED RED; LED_1206
J1: HEADER_1x03; PinHeader_1x03_P2.54mm_Horizontal
J2, J3: SM04B-GHS-TB; JST_GH_SM04B-GHS-TB_1x04-1MP_P1.25mm_Horizontal
Me: HOLE; MountingHole_3mm
R1: 470R; SMD-0603
R2, R3, R5: 10k; SMD-0603
R4: 180R; SMD-0603
R6: 0R; SMD-0603
R7, R8: -; SMD-0603
R10: 100R; SMD-0603
U1: PCF8583; SOT176-1
U2: 74AHC1G14GV; TSOP-5_1.65x3.05mm_P0.95mm
U3: MIC5504-3.3YM5; SOT-23-5

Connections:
+3V3: C1.1, C5.1, C6.1, R2.1, R3.1, R7.1, R8.1, U1.8, U2.5, U3.5
+5V: C3.1, C4.1, D1.1, J2.1, J3.1, R6.1, U3.1, U3.3
/COUNT: J1.1, R1.2, U2.2
/SCL: J2.2, J3.2, R2.2, U1.6
/SDA: J2.3, J3.3, R3.2, U1.5
GND: C1.2, C2.2, C3.2, C4.2, C5.2, C6.2, D1.2, D2.1, J1.3, J2.4, J2.MP, J3.4, J3.MP, Me.1, R5.2, U1.4, U2.3, U3.2
unnamed: C2.1, J1.2, R10.1
unnamed: D2.2, R4.2
unnamed: R1.1, R6.2, R8.2, R10.2
unnamed: R4.1, U1.1, U2.4
unnamed: R5.1, R7.2, U1.3

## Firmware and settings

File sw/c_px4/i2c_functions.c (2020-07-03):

#include "i2c_functions.h"

#include <linux/i2c-dev.h>
#include <i2c/smbus.h>
#include <fcntl.h>
#include <sys/stat.h>
#include <sys/ioctl.h>
#include <stdio.h>
#include <stdlib.h>
#include <unistd.h>

//from https://www.kernel.org/doc/Documentation/i2c/dev-interface

//I2C
int file;
int gaddr;

void i2c_open(int bus, int addr)
{
   gaddr=addr;

   char filename[20];

   snprintf(filename, 19, "/dev/i2c-%d", bus);
   file = open(filename, O_RDWR);

   if (file < 0) 
   {
       fprintf(stderr, "Chyba otevření: %s \n",filename);
       exit(1);
   }

   if (ioctl(file, I2C_SLAVE, addr) < 0) 
   {
       fprintf(stderr, "Chyba nastavení adresy : 0x%x \n", addr);
       exit(1);
   } 
}

void i2c_close()
{
   close(file);
}

/*void transfer(uint8_t *send, int sendlen, uint8_t *rcv, int rcvlen)
{
     if (file < 0) 
     {
         fprintf(stderr,"soubor neotevřen\n");
     }

     int ret;
     if(send!=NULL)
     {
        ret=write(file,send,sendlen);
        if(ret!=sendlen)
            fprintf(stderr,"chyba zápisu: %d\n", ret);
     }
     if(rcv!=NULL)
     {
        ret=read(file, rcv, rcvlen);
        if(rcvlen!=ret)
            fprintf(stderr,"chyba čtení: %d\n",ret);
     }
}*/

void transfer( uint8_t *send, unsigned send_len, uint8_t *recv, unsigned recv_len)
{

	struct i2c_msg msgv[2];
	unsigned msgs;

	msgs = 0;

	if (send_len > 0) {
		msgv[msgs].addr = gaddr;
		msgv[msgs].flags = 0;
		msgv[msgs].buf = send;
		msgv[msgs].len = send_len;
		msgs++;
	}

	if (recv_len > 0) {
		msgv[msgs].addr = gaddr;
		msgv[msgs].flags = I2C_M_RD;
		msgv[msgs].buf = recv;
		msgv[msgs].len = recv_len;
		msgs++;
	}

	if (msgs == 0) {
		return;
	}

	struct i2c_rdwr_ioctl_data packets;

	packets.msgs  = msgv;

	packets.nmsgs = msgs;

   int ret = ioctl(file, I2C_RDWR, (unsigned long)&packets);
   if (ret == -1) 
   {
				fprintf(stderr, "transfer failed\n");

	} 

}


//I2C -registrs
void setRegister(uint8_t reg, uint8_t value)
{
      uint8_t buff[2];
      buff[0]=reg;
      buff[1]=value;
      transfer(buff, 2, NULL, 0);

}

uint8_t readRegister(uint8_t reg)
{
      uint8_t rcv;
      transfer(&reg, 1, &rcv, 1);
      return rcv;
}

/*void 
setRegister16(uint8_t reg, uint16_t value)
{
      printf("check endians first...");
      uint8_t buff[3];
      buff[0]=reg;
      buff[1]= (uint8_t)((value & (uint16_t) 0xFF00) >> 8); //TODO: check indians 
      buff[2]=(uint8_t)( value & (uint16_t) 0x00FF);      
      transfer(buff, 3, NULL, 0);
}*/

uint16_t 
readRegister16(uint8_t reg)
{
      uint8_t rcv[2];
      transfer(&reg, 1, rcv, 2);
      //printf("%x %x =>",rcv[0], rcv[1]);
      uint16_t ret=0x0;
      ret=rcv[0]<<8 | rcv[1];
      //printf("%x\n",ret);
      return ret;
}

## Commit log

2019-12-02 sch edit
    [TFRPM01A.kicad_pcb, TFRPM01A.sch]
2019-12-10 Úprava popisků.
    [TFRPM01A.kicad_pcb]
2019-12-10 Silkscreen improvement move texts to avoid crossing vias.
    [TFRPM01A.kicad_pcb]
2019-12-12 zmena vrstvy
    [TFRPM01A.kicad_pcb]
2019-12-19 Generate images
    [TFRPM01A.kicad_pcb]
2019-12-19 Edit PCB
    [TFRPM01B.kicad_pcb, TFRPM01B.sch]
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2020-01-30 New case for RPM sensor
    [RPM_case.scad, RPM_case.stl]
2020-01-30 update dimensions
    [RPM_case.scad, RPM_case.stl]
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2020-02-06 uprava podle issue
    [RPM_case.scad, RPM_case.stl, TFlogo.scad]
2020-06-15 Vyrobni data PCB
    [TFRPM01B-B_Cu.gbr, TFRPM01B-B_Mask.gbr, TFRPM01B-Edge_Cuts.gbr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]
2020-06-24 Edit U2
    [TFRPM01B.sch]
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2020-12-09 Attempt to resolve #3. Library is not actually used, because it does not have proper functionalities.
    [RPM_case.scad, parameters.scad]
2020-12-09 Swap text to outer relief instead of inner. #8
    [RPM_case.scad, RPM_case.stl]
2020-12-11 Increase depth/height of marking #8
    [RPM_case.scad]
2020-12-11 Improve PCB fit to the case.
    [RPM_case.scad]
2020-12-15 Fix printability of texts and symbols.
    [RPM_case.scad, RPM_case.stl]
2020-12-15 Imroved printing of the logo. Removed relief texts.
    [RPM_case.scad, RPM_case.stl, parameters.scad]
2020-12-15 Fix screw position dimensions. Fix mounting screm position in the box.
    [RPM_case.scad, RPM_case.stl, TFRPM01B.kicad_pcb]
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2020-12-21 Removing the relief texts from PCB cover.
    [RPM_case.scad, RPM_case.stl]
2021-01-23 Změna formátu.
    [TFRPM01B.kicad_sch]
2021-01-23 Title block updated to TF version.
    [TFRPM01B.kicad_sch, TFRPM01B.sch]
2021-02-17 #12 #5 #4
    [TFRPM01B.kicad_pcb, TFRPM01B.kicad_sch]
2021-02-18 Úprava PCB
    [TFRPM01C.kicad_pcb, TFRPM01C.kicad_sch]
2021-02-18 Edit, generate images
    [TFRPM01C.kicad_sch]
2021-02-18 Edit labels PCB
    [TFRPM01C.kicad_pcb]
2021-02-18 uprava krabicky - pro delsi sroub
    [RPM_case.scad, RPM_case.stl]
2021-02-19 Generation of production data
    [TFRPM01B-B_Cu.gbr, TFRPM01B-B_Mask.gbr, TFRPM01B-F_Cu.gbr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]
2021-02-19 Testing of PCB size increase by 1mm in each direction.
    [RPM_case.stl, parameters.scad]
2021-02-19 Zapusteni matky
    [RPM_case.scad]
2021-02-24 Uprava soucastek ve schema
    [TFRPM01C.kicad_sch]
2021-03-05 samolepka v openscadu
    [RPM_case.scad, TFRPM.blend]
2021-03-13 zobrazeni stitku v modelu
    [RPM_case.scad]
2021-03-13 Removed experimental increase of case for PCB.
    [parameters.scad]
2021-03-13 Doplnění aktuálních součástek pro osazení.
    [TFRPM01C.kicad_sch]
2021-03-17 uprava krabicky pro tisk
    [RPM_case.scad, RPM_case.stl]
2021-03-19 Edit schema
    [TFRPM01C.kicad_sch]
2021-03-19 Edit schéma
    [TFRPM01C.kicad_sch]
2021-03-19 Reseni #20, #19, #18
    [RPM_case.scad, RPM_case.stl]
2021-03-19 pridani dalsich zkoseni u LED a u matice #18
    [RPM_case.stl]
2021-03-19 Oprava zkoseni, #18
    [RPM_case.scad, RPM_case.stl]
2021-03-19 Improve solution of issue #19
    [RPM_case.scad, RPM_case.stl]
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2021-03-23 PCB dimensions image updated to current version.
    [TFRPM01C-B_Cu.gbr, TFRPM01C-B_Mask.gbr, TFRPM01C-B_Silkscreen.gbr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]
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2021-03-24 řešení #23, #20, - změna tloušťky víčka, posun hrany nad rezstorem R1
    [RPM_case.scad, RPM_case.stl]
2021-03-25 Improve centering of screw to case depth.
    [RPM_case.scad, RPM_case.stl, TFlogo.scad]
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2021-04-03 Resolve #25 Nut shifted by 0.5 + layer thickness outer of the box.
    [RPM_case.scad, RPM_case.stl]
2021-04-05 Reference the title block from the submodule.
    [TFRPM01C.kicad_sch]
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2021-07-30 Fix bridge thickness at bottom side of the box. Improve fit of top and bottom part.
    [RPM_case.scad, RPM_case.stl]
2021-07-30 Multi instance g-code generation.
    [RPM_case_Prusa_project.3mf]
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2022-01-30 update to newest kicad version, set schematic tempate, clean dps
    [TFRPM01C.kicad_pcb, TFRPM01C.kicad_sch]
2022-03-05 Generate paste layer
    [TFRPM01C.kicad_pcb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]
2022-03-15 Automated Change
    [TFRPM01C.kicad_pcb]
2022-03-16 vycisteni repozitare, prejmenovani na verzi D
    [TFRPM01C.kicad_pcb, TFRPM01C.kicad_sch, TFRPM01D.kicad_pcb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]
2022-03-16 Upraveni PCB, pridani popisku, vyresení #21, #26, urava silkscreenu, vypocet polohy led v openscadu
    [RPM_case.scad, TFRPM01D.kicad_pcb]
2022-03-16 Push actions product
    [TFRPM01C-B_Cu.gbr, TFRPM01C-B_Mask.gbr, TFRPM01C-B_Paste.gbr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]
2022-03-29 update action, clean repo
    [TFRPM01D-B_Courtyard.dxf, TFRPM01D-B_Cu.dxf, TFRPM01D-B_Fab.dxf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]
2022-03-29 procisteni dat
    [TFRPM01D.kicad_pcb, TFRPM01D.kicad_sch]
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2022-07-20 LED case bug fix
    [TFRPM01D.kicad_pcb]
2022-09-19 Výměna pouzder LED a D zener
    [TFRPM01D.kicad_pcb, TFRPM01D.kicad_sch]
2022-09-26 Edit PCB. LED footprint. 10uF 0805 to 0603
    [TFRPM01D.kicad_pcb, TFRPM01D.kicad_sch]
2022-09-28 Graphics and layout improvements. Net classes for default and power set.
    [TFRPM01D.kicad_pcb, TFRPM01D.kicad_sch]
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2022-10-03 Improve layout uniform track widts. Resolve DRC and ERC issues.
    [TFRPM01D.kicad_pcb, TFRPM01D.kicad_sch]
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2022-10-03 Move JP1 far away from TF logo.
    [TFRPM01D.kicad_pcb]
2022-10-03 Move trace to avoid sharp angles.
    [TFRPM01D.kicad_pcb]
2022-10-03 reduced thickness of text.
    [TFRPM01D.kicad_pcb]
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2023-03-05 update case for 01D
    [RPM_case.scad, RPM_case.stl, TFRPM01D.kicad_pcb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]
2023-05-05 Update nut dimensions and tolerances
    [RPM_case.scad, RPM_case.stl, RPM_case_Prusa_project.3mf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]
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2023-05-07 Update PCB dimensions image.
    [TFRPM01.kicad_pcb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]
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2023-05-26 Exclude Fiducial + SolderJumper_3_Bridged12 + M3 from BOM.
    [TFRPM01.kicad_sch]
2023-05-26 Update part number marking.
    [TFRPM01.kicad_sch]
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2023-05-26 Upgrade PCB from schematics. Minor layout improvement of sharp track in case of LED and U2 pads.
    [TFRPM01.kicad_pcb, TFRPM01.kicad_sch]
2023-05-31 try to remove holes support
    [RPM_case.scad, RPM_case.stl]
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2023-06-01 Change type marking of pin_header.
    [TFRPM01.kicad_sch]
2023-06-01 Upgrade PCB from schematics.
    [TFRPM01.kicad_pcb]
2023-06-13 Update LEDs part numbers.
    [TFRPM01.kicad_pcb, TFRPM01.kicad_sch]
2023-06-14 Updated year mark in silkscreen.
    [TFRPM01.kicad_pcb]
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2024-05-02 Update KiCAD project. Add spreadsheet to calculate voltage tresholds.
    [TFRPM01.kicad_sch, Treshold_interpolation.ods]
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2024-05-30 Update schematics symbols and PCBs to resolve errors in action run.
    [TFRPM01.kicad_pcb, TFRPM01.kicad_sch]
2024-11-01 Update testing script. Attempt to fix new python3 dependencies.
    [TFRPM01.kicad_sch]
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2024-11-07 Modify code to stay in curses even in case of error.
